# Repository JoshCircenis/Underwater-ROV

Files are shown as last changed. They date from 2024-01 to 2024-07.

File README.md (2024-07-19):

# Underwater-ROV
## Table of Contents
* [About](#About)
* [Overview](#Overview)
  * [Lateral Control](<#Lateral-Control>)
  * [Depth Control](<#Depth-Control>)
  * [Hull](<#Hull>)
  * [Communication](<#Communication>)
* [Improvements](#Improvements)

## About
The goal of this project is to create a fully functional underwater ROV without spending a lot of money. This means that the ROV should be able to move freely horizontally and vertically throughout a body of water and should be able to send and record live video.

## Overview

#### Lateral Control
To move freely in a body of water most ROVs use thrusters in a variety of configurations for maneuverability. There are three commonly used configurations for ROV propulsion each of which has its own influence on the power, electronics, and number of thrusters needed to function. The first configuration utilizes two thrusters in the same orientation situated on each side of the ROV as shown below.

two thruster propulsion two thruster propulsion maneuverability

This configuration uses differential control for turning and drives both thrusters at the same level for forward and reverse. The benefit of this propulsion configuration is that it is very simple in terms of thrusters, electronics, and power. The main drawback is that this configuration is less maneuverable and generally less powerful than other configurations. To improve maneuverability the thrusters can be installed at an angle, this improves the turning ability but can reduce the forward and reverse thrust.

The second configuration utilizes three to four thrusters where two are placed in the same configuration as the previous, but additional thrusters are placed perpendicular to the first set as shown below.

three thruster four thruster

This configuration requires more power and electronics because there are more thrusters but it is more powerful and maneuverable than the previous configuration.

The third configuration utilizes four thrusters which are all placed at an angle around the ROV as shown below.
four thruster angled

This configuration is a balance between having full maneuverability and power. In this configuration, depending on the mixing, all motors can be used for both forward and reverse thrust and for turning. However, this configuration is more complicated in terms of implementation and rc control.

After reviewing all of these propulsion configurations, I decided to use the first configuration with two motors. This is because for this ROV a key part of the goal is to keep down cost and complexity. To achieve this I was able to find a dual-motor brushed ESC that included the motors, shafts, and propellers. This product is designed for RC boats but with the proper construction, it should function properly on the ROV. The main problem with using these motors is that unlike brushless motors it is not optimal to run these motors directly in the water, although it can be done this will decrease performance and increase the wear on the motors. So, I will be utilizing stuffing box which will allow the motor to be mounted internally and the shaft will pass through the stuffing box and into the water preventing water from flowing around the shaft into the ROV. However, while this works well to waterproof a shaft for a boat, the ROV will be at depth which will put pressure on the seal and could cause leaking. To avoid any issues associated with this I will also be placing the motors in two isolated nacelles on each side of the ROV so that even if the seal leaks all of the electronics will be isolated so the damage is minimized.

#### Depth Control
The most common method of depth control in an ROV is using vertical thrusters to controll the depth of a neutrally buoyant ROV. However, another way to do achieve vertical controll is by utilizing variable ballast tanks to control the ROV's density and therefore its buoyancy. I decided to utilize the second method and incorporate ballast tanks into the ROV, because I believe it will be possible to design the tanks such that they are very cheap and it would allow for a more streamlined design. I was originally planning on using linear actuators to pull and push 50mL syringes which would pull in and push out water to change the weight. However, after doing some research into different designs I found that it would be cheaper and possibly more accurate to instead convert a regular 9g servo into a linear servo which could accurately position the syringe. To do this I swapped the motor in a 9g servo with a motor that operates on a similar voltage but is heavily geared to handle the load that it would experience when moving the syringe. This motor was coupled to a lead screw which would pull and push a captive nut in a custom 3D-printed syringe plunger which also moved a linear potentiometer to tell the servo its current position. Additionally, two 10k rotational potentiometers were included to adjust and fine-tune the travel of the syringe, and two thrust bearings were included on each side of the shaft coupler to transfer the load from the motor to the 3D-print which improves operation. This video shows the linear servo moving the syringe and automatically slowing down and stopping, the movement of the motor in the video is due to not adjusting the shaft coupler set screws evenly and it won't occur in the final ROV. 

https://github.com/JoshCircenis/Underwater-ROV/assets/98178221/2553f830-2ba3-4c8f-8b04-3c350286e0a8

The final ROV will have two of these allowing for 50mL of water to be displaced. This solution cut down the cost and complexity a lot because each tank can simply be driven as a regular servo and the components used to create the tanks were inexpensive. Additionally, the ROV will have two of these tanks, one on each end, which will allow for pitch control by moving the center of mass of the ROV between the two tanks.

#### Hull
Many ROVs use a frame design where a PVC frame holds all of the components of the ROV. However, because of the motors that I am using, I decided to go for a more hydrodynamic and streamlined design to reduce drag. Additionally, I would like to minimize the amount of material necessary for the hull by reducing complexity. Because of this, I decided to use three feet of 4" schedule 40 PVC pipe to house everything except for the motors which will be in two smaller side nacelles as previously stated. This will keep down the cost and complexity while still creating a functional and pressure-resistant hull. Also, to improve footage recorded from the ROV the front will have a clear dome which will allow for a greater field of view for the cameras. Below is a 3D model that outlines the structure and is similar to how it should look once completed

ROV

#### Communication
To control the ROV I plan on using an FS-I6 rc transmitter and an FS-IA6B rc receiver. But, 2.4 GHz, which is the most common RC frequency, only penetrates a few centimeters through water so simply putting a receiver on the ROV won't allow for any significant depth to be reached. It is possible to use a receiver and transmitter with lower frequencies but those cost more and a wireless system prevents live video transmission which would make it hard to navigate at depth. To get around these problems the ROV will have a tether to the surface of the water. For the tether, I am using 100 feet of CAT5 ethernet cable because it is easy to get and will have more than enough wires to control the ROV. The tether will connect to the ROV with an underwater ethernet port so that the tether and float can be disconnected when not in use or to swap tethers. The FS-IA6B has PPM capability which will encode all of the channels that the receiver has and send it over a single line through the tether to the ROV where it will be connected to a PPM decoder which has all of the necessary PWM ports for the motors and servos. Additionally, a video transmitter for FPV drones will be in the float and the video signal will run from the camera in the ROV through the tether to the float. This will provide live video for piloting the ROV, additionaly a RunCam will also be on the ROV to record higher-quality footage that can be viewed later. With this setup, it is also necessary for the float and the ROV to each have their own onboard batteries to avoid losses in transmitting power over the tether. The float will have a 2s (7.4V) 900mAh lipo battery because it only has to support the RC receiver and the video transmitter and the ROV will have a 2s 4000mAh lipo battery to support all of the electronics on the ROV. Because of this, it is also necessary to connect the ground of the float and ROV using the tether because the signals being sent over the tether are ground-referenced.

Below is a photo of all of the components for both the ROV and the float laid out.



## Improvements
Since this project has not been completed yet I am not sure about improvements that need to be made, but I am suspicious of the shaft seals and power. Because the motors that I am using are made for a boat that is smaller and has less drag I am concerned about the ROV being extremely slow. Also, I am planning on using a tube filled with grease that goes around the shaft with a tight tolerance to seal the drive shaft but this might not work at depth. It is not a huge issue if it leaks because the motors shouldn't be badly damaged by temporary submersion in water and they are completely isolated from the main tube so it won't damage the electronics. However, it could cause issues with the vertical control by compressing the air in the nacelles and changin the density. I have some preemptive ideas that could fix it, such as 3D printing a complicated grease trap that incorporates several O-rings or adding a flexible membrane to the nacelle to equalize pressure during the dive. But the stuffing box with O-ring seals should work and I will have to wait till the first test to see if the original plan works before implementing one of the aforementioned solutions.

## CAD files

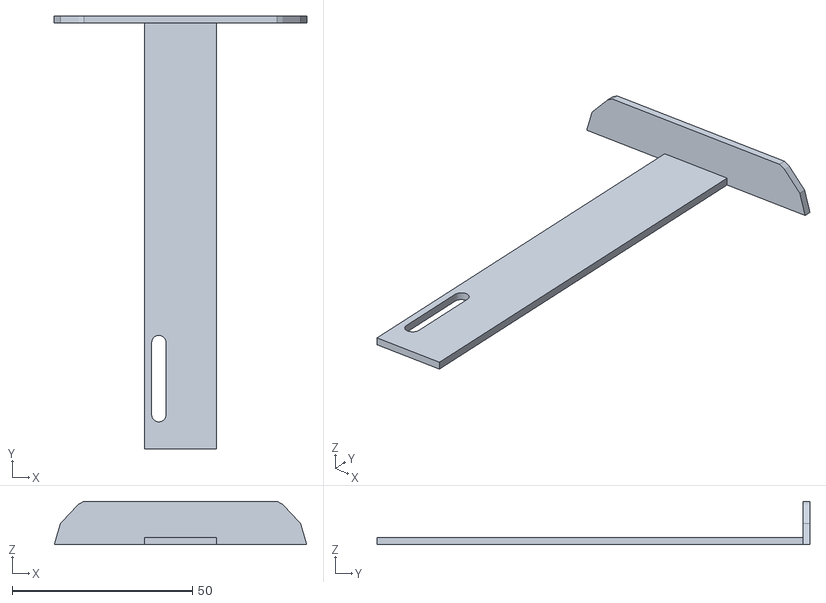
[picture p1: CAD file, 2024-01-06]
models/Linear Potentiometer mount.stl
70.0 x 120.0 x 12.0

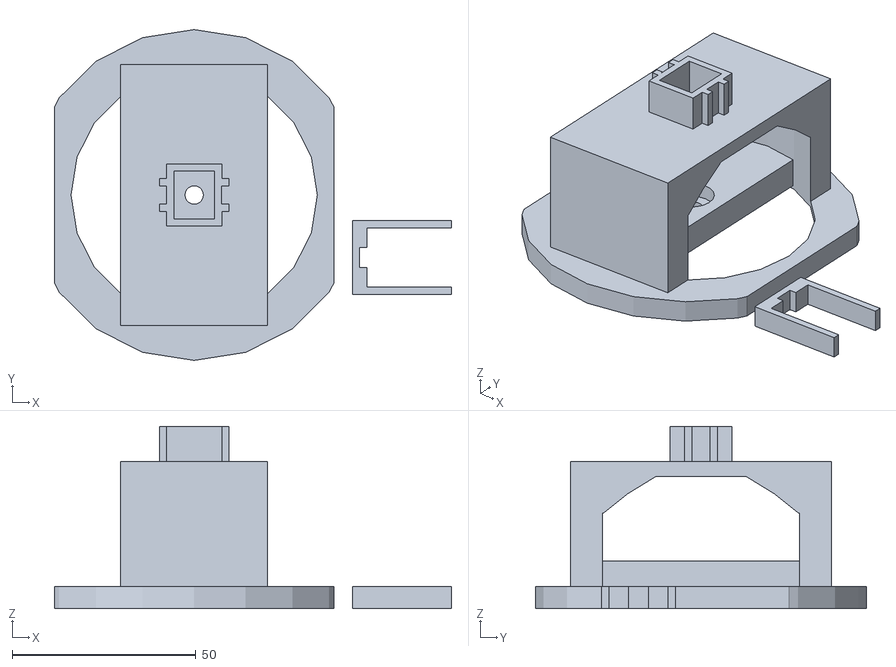
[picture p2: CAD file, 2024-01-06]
models/Syringe motor attachment.stl
108.0 x 90.0 x 49.6

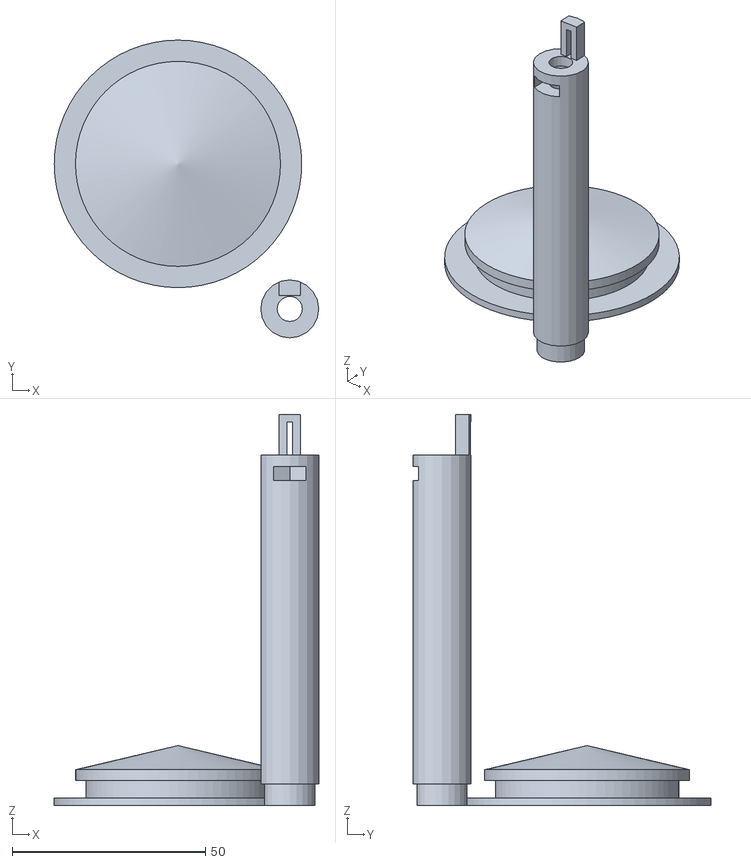
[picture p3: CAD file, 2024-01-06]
models/Syringe Plunger.stl
68.4 x 77.0 x 101.1
